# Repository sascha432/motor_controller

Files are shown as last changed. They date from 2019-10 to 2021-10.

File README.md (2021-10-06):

# DC Motor Controller with LED dimmer

Firmware for DC motor controller https://easyeda.com/sascha23095123423/dc-motor-controller

I am using this controller for a 500W drill press with a constant RPM from 300-4500rpm load independent

* Input voltage 13.5-40V
* DC Motor controller 20A continuously, 31.25kHz PWM
* 4A MOSFET driver
* Velocity mode, constant RPM from 150 up to 32000rpm
* PWM mode, duty cycle 5-100% (like regular drills)
* Opto Interrupter for RPM sensing
* Adjustable current limit 1-40A
* Adjustable auto stop if stalled for 250-5000ms
* Brake function with slow current decay
* ATmega328P PID controller for constant RPM
* LED driver 14-26V, 350mA, 10W, dimmable
* OLED display and rotary encoder, start/stop button
* Continuous motor current measurement and display (Ampere or Watt)
* Current limit indicator LED

## New Firmware 1.0.4

[Change Log v1.0.4](docs/CHANGELOG.md)

### Current PCB

[Schematics and Gerber Files](schematics/)

[https://oshwlab.com/sascha23095123423/dc-motor-controller](https://oshwlab.com/sascha23095123423/dc-motor-controller)
[https://oshwlab.com/sascha23095123423/dc-motor-controller-panel](https://oshwlab.com/sascha23095123423/dc-motor-controller-panel)

### Change Log PCB

### Rev1.4 & Rev1.5

* Motor current measurement
* MOSFET for the brake
* Improved DAC and current limit
* Improved LED dimmer
* IDC connector for the control panel (2x5P)
* JST PH connectors
* DTR connection for AVRDude/USB2Serial converters

### Rev1.3

* Current limit indicator LED
* Hardware circuit for current limit removed and overcurrent signal added to the MCU
* UCC27517DBVR MOSFET driver
* Kelvin connection to the shunt

### Rev1.1 & 1.2

* Input voltage detection
* PCB layout changes

### Rev1.0

* First prototype

## PCB and schematics

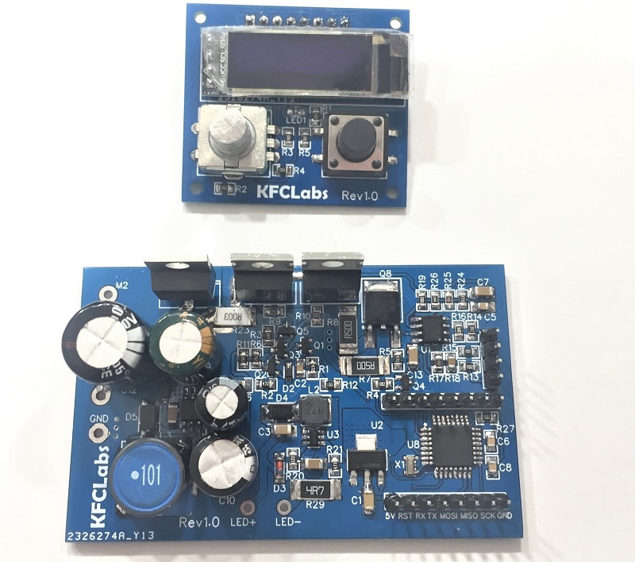
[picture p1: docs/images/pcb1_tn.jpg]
PCB Rev1.0


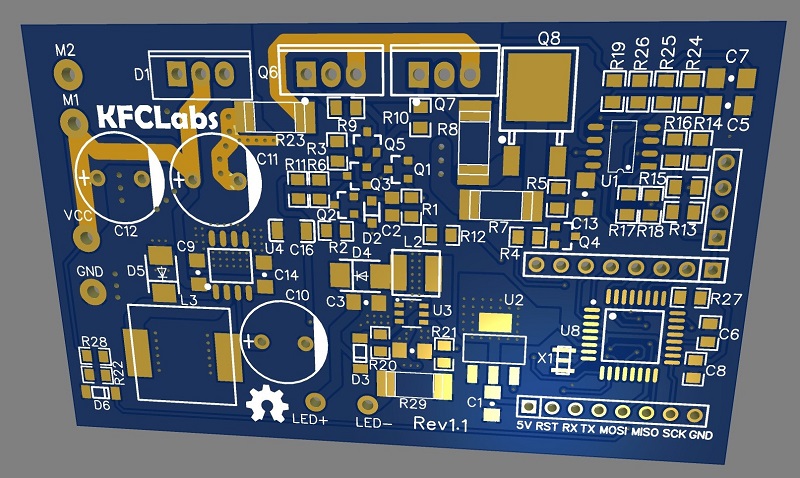
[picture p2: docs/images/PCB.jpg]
PCB


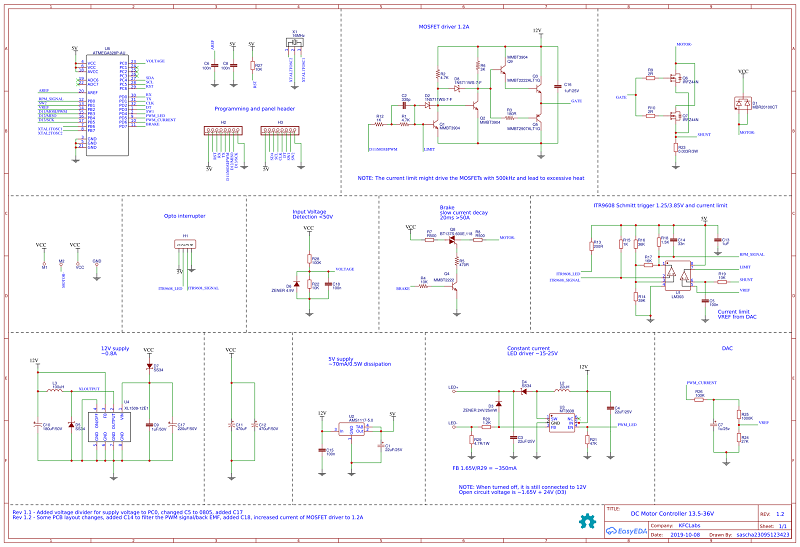
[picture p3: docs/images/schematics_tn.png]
Schematics


## First breadboard prototype

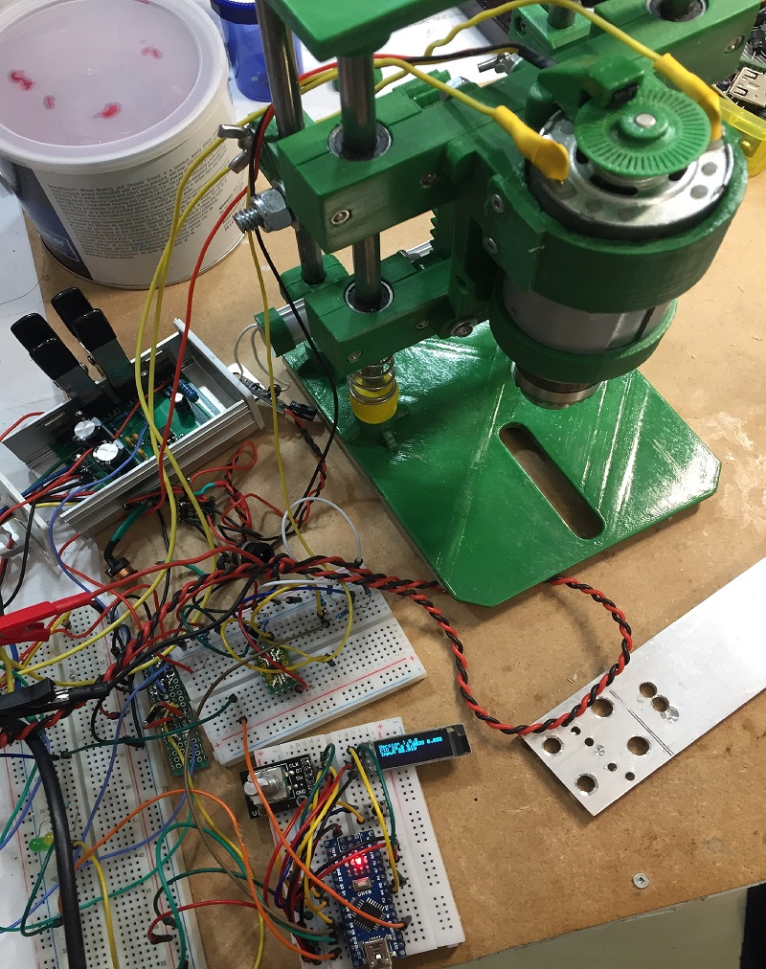
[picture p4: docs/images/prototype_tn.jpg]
Prototype


## STL files for the drill press

[Remix of a great drill press](https://www.thingiverse.com/thing:3693804)

[STL download](https://raw.githubusercontent.com/sascha432/motor_controller/master/stl/drill_press_stl.zip)

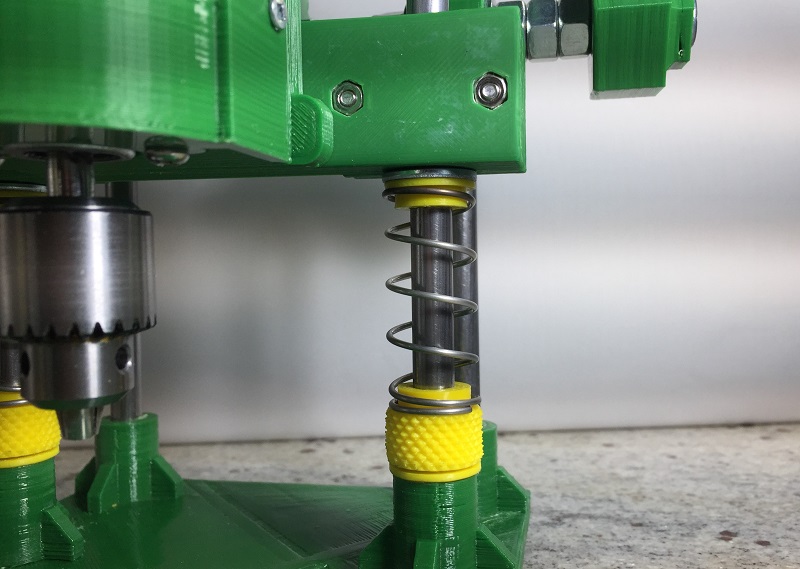
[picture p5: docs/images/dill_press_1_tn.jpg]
Drill press 1


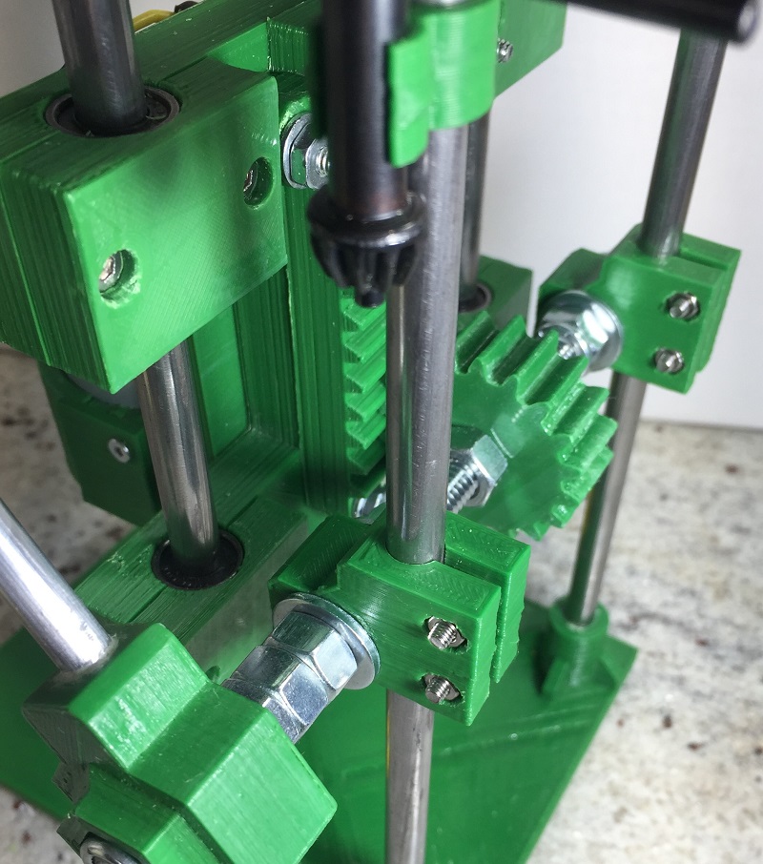
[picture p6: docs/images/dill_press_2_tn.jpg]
Drill press 2


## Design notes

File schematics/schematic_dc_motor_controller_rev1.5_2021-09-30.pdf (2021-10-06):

D11/MOSI/PWM

BRAKE

MOTOR-

IRF3205

Q6

IRF3205

Q7

GATE

6R

R9

6R

R10

GATE

MOTOR-

LM393

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
ITR9608_SIGNAL

ITR9608_LED

1K

R15
100R

R13

47K

R14

47K

R16

200K

R17

4.7K

R18

RPM_SIGNAL

M1

M2

16MHz

X1

1

2

3
XTAL2TOSC2

XTAL1TOSC1

AREF

5V
5V

100nF

C8
100nF

C6
33K

R27

XTAL2TOSC2

XTAL1TOSC1

AREF

5V

D13/SCK

D12/MISO

D11/MOSI/PWM

RST

TX

RX

ATMEGA328P-AU

U8

VCC 4
VCC 6
AVCC 18

ADC6 19
ADC7 22

AREF 20

PB0 12
PB1 13
PB2 14
PB3 15
PB4 16
PB5 17
PB6 7
PB7 8

GND 3
GND 5
GND 21

PC0 23
PC1 24
PC2 25
PC3 26
PC4 27
PC5 28
PC6 29

PD0 30
PD1 31
PD2 32
PD3 1
PD4 2
PD5 9
PD6 10
PD7 11

RPM_SIGNAL

SCL

SDA

CLK
DT
SW1

AMS1117-5.0

U2

In 3 | Out 2 GND

1

TAB 4

12V

22uF

C1

VCC

VCC

GND

4.7uF/50V

C3

MT3608

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
SS34

D4

12V

100K

R20
PWM_LED

47K

R21

LED-

LED+

I got the best results with 4.7uF, LEDs 21.6V@250mA and 120, 180 or 240Hz. With higher frequencies the dimming curve becomes non linear and the increase from duty cycle 96-100% is pretty steep (current 70-100%). There is no visible flicker and most cameras can filter multiples of 60Hz.
Using a lower output capacitor leads to overshoot at each PWM cycle
D6 is optional to prevent damage from overshoot. If the output capacitor is
too small, the diode will heat up.

22uF/25V

C4

22uH

L2

0.008R/3W

R23

10K

R19
SHUNT

VREF

VREF

10K

R25
100K

R26

PWM_CURRENT

10uF

C7

5V

XL1509-12E1

U4

VIN

1
OUTPUT

2

FB

3
ON/OFF

4 GND

5

GND

6

GND

7

GND

8

1uF/50V

C9
SS34

D5
180uF/50V

C10

12V | VCC

470uF

C11
470uF/50V

C12

XLOUTPUT

VCC

SHUNT

100uH/2A

L3

SBT40100VCT

D1

MOTOR-

VCC

1uF

C13

10uF

C16

SW2

PWM_LED
PWM_CURRENT
BRAKE

VREF

Brake / slow current decay
Adjust R8 that the current stays below the max. ratings of the MOSFET and motor

DAC for current limit detection
0-318mV, ~30 V ripple
200-300ms to reach the max. voltage @ 980Hz

MOSFET driver 4A

5V supply
~70mA/0.5W dissipation

12V supply
~110mA
With 10W of LEDs it goes up to 1.3A
If the LED driver is not used, it only requires a small inductor

ZENER 24V
D3

VCC

The original current limiter has been replaced and the LM393 sends a signal to the MCU. The rise time is <0.5ms

Current limit
VREF from DAC

VOLTAGE

Rev 1.1 - Added voltage divider for supply voltage to PC0, changed C5 to 0805, added C17
Rev 1.2 - Some PCB layout changes, added C14 to filter the PWM signal/back EMF, added C18, increased current of MOSFET driver to 1.2A, optional pullup R11 Rev 1.3 - Low cost 4A MOSFET driver UCC27517DBVR, Replaced R7 and R8 since they could not handle the braking current, replaced zener D6 with R31,
removed current limit circuit, connected current limit detection to D12/MISO, added proper trace from shunt to LM393, moved MOSFET driver away from shunt for better cooling, added LED output to PC1 Rev 1.4 - Improved LED dimming, current limit sensing and DAC, TO-220 TRIAC, C14 to filter noise from the opto interrupter
Rev 1.5 - Different connector for the control panel, JST PH wire to board connectors, removed R11, added PC3/ADC3, PE2/ADC6, PE3/ADC7 to headers, changed TRIAC brake to MOSFET, connection for DTR

VOLTAGE

VCC

2.7K

R22

100K

R28

Input Voltage Detection

Programming and panel header

Opto interrupter

A | A
B | B
C | C
D | D
E | E
F | F

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
TITLE:
DC Motor Controller 12-40V, 20A | REV: 1.5
Date: | 2019-10-08

Sheet: 1/1
Drawn By: sascha23095123423

Company: KFCLabs

100nF

C15

VCC

220uF/50V

C17

10nF

C18

NOTE: When turned off, it is still connected to 12V Open circuit voltage is ~26V

12V

MOTOR-

SHUNT

100nF

C2

UCC27517DBVR

U5

VDD 1
GND 2
IN+ 3
IN- 4
OUT 5

10K

R1

10K

R6

100K

R31

1R/5W

R8

10nF

C5

D12/MISO

4.7K

R4

Schmitt trigger for ITR9608 with 2.24/2.76V and current limit sensing

The current limit is supposed to signal over current to the MCU, not limit the actual current.

R9/10 limit the current to 4A @ 12V

LIMIT_LED

LIMIT_LED

300R

R7

31.25kHz PWM

# DC Motor Controller

- 13.5(12)-40V, 20A

## - Current limit sensing - 10W LED driver - Support for RPM measurement - PID controller for constant RPM

1uF

C20
6.8K

R12

1K

R24

100nF

C21

5.1R

R29
5.1R

R30
5.1R

R32

SHUNTMEAS

SHUNTMEAS

Optional constant current LED driver ~15-25V, PWM up to 1kHz

1nF

C14

BZT52C33

D6

RST

BSS138

MOTOR- | Q3

SS34

D2

### Remote Control Panel (OLED display, rotary encoder and buttons) https://oshwlab.com/sascha23095123423/dc-motor-controller-panel

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
9 10 10

5V

RST
RX
TX

D11/MOSI/PWM
D12/MISO
D13/SCK

B6B-PH-K-S(LF)(SN)

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
ITR9608_LED
ITR9608_SIGNAL

B10B-PH-K-S-(LF)(SN)

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
10 10

PC3

ADC7

ADC6

ADC6

PC3

ADC7

200K

R2

220K

R3

10K

R5

ZENER 15V

D7

IRF9540NPBF

Q1

DTR

DTR

10uF

C19

RST

DTR is for AVRDude/USB2Serial converters
If the reset pulse is too short, increase R27 and decrease it, if it is too long

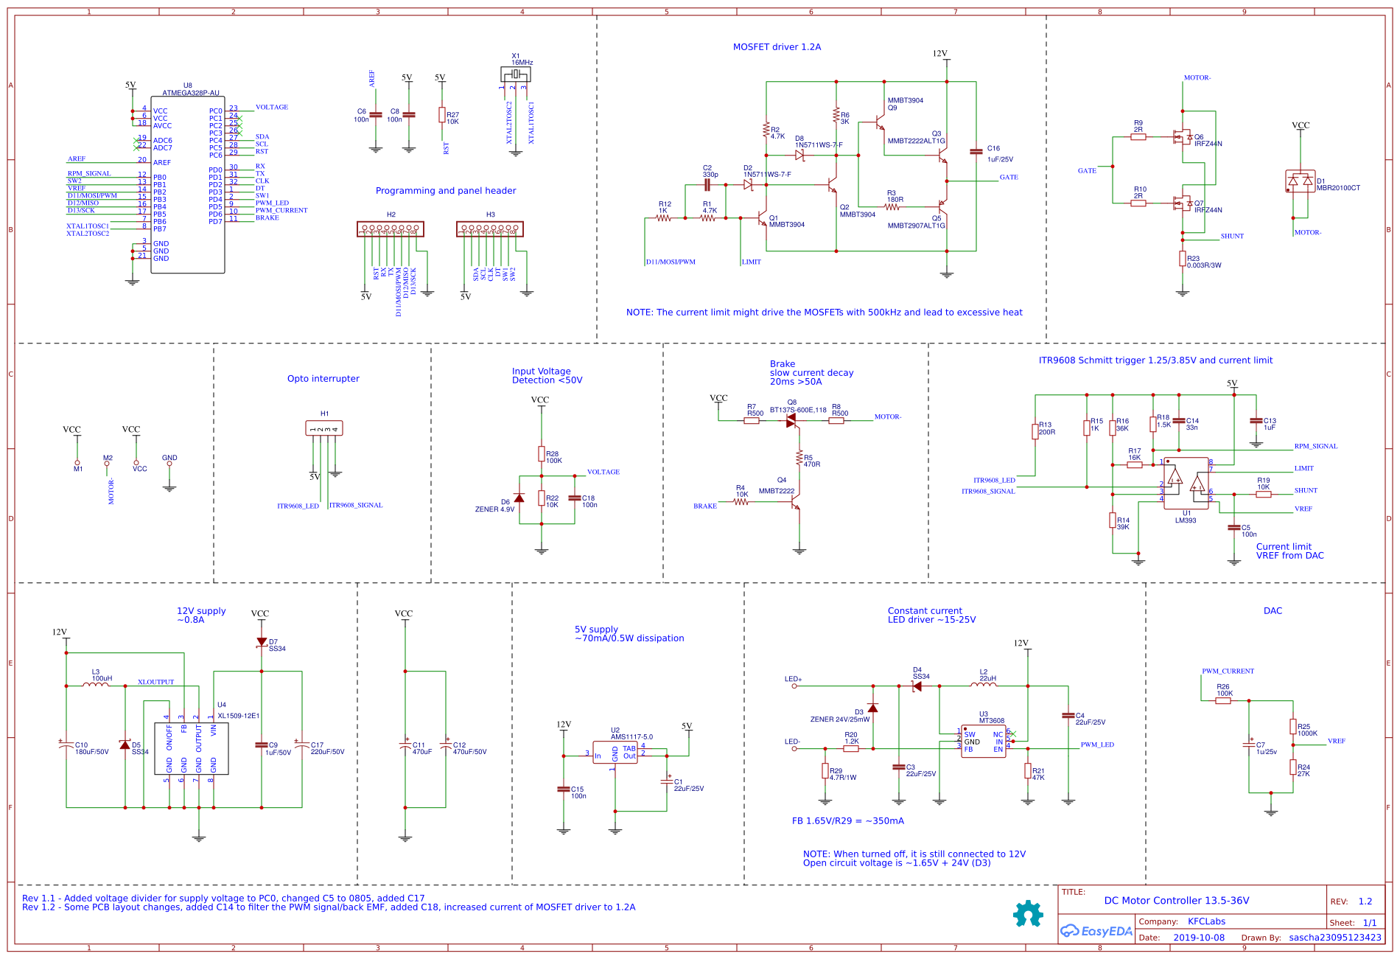
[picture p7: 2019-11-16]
docs/images/schematics.png

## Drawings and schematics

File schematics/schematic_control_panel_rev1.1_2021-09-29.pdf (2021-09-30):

## Control Panel with OLED display, rotary encoder and 2 buttons

## 5VSW¹ SW²

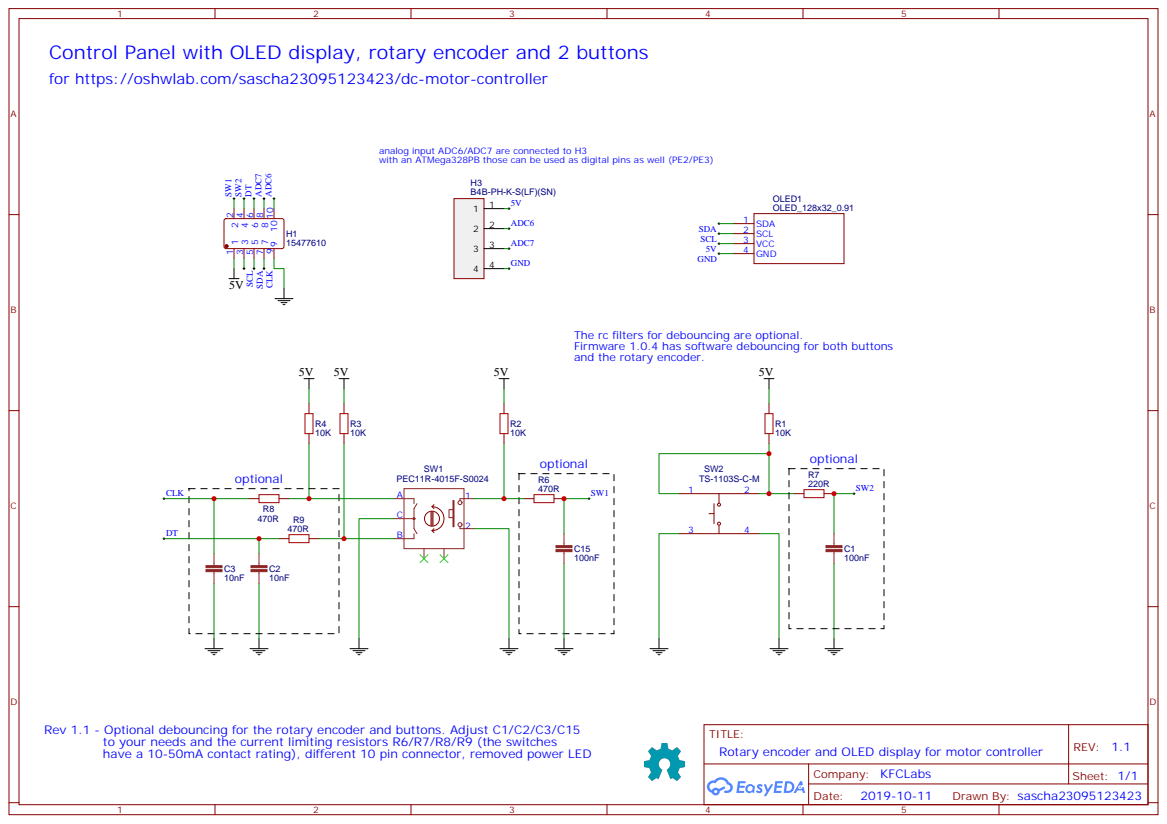
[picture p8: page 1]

for https://oshwlab.com/sascha23095123423/dc-motor-controller

analog input ADC6/ADC7 are connected to H3
with an ATMega328PB those can be used as digital pins as well (PE2/PE3)

The rc filters for debouncing are optional.
Firmware 1.0.4 has software debouncing for both buttons
and the rotary encoder.

Rev 1.1 - Optional debouncing for the rotary encoder and buttons. Adjust C1/C2/C3/C15

TITLE:
Rotary encoder and OLED display for motor controller

to your needs and the current limiting resistors R6/R7/R8/R9 (the switches
have a 10-50mA contact rating), different 10 pin connector, removed power LED

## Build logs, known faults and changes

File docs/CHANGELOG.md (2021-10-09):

# Changelog

## 1.0.5-dev

  - Fixed PWM mode running in velocity mode
  - Inverted current limit signal to match PCB Rev1.5
  - Improved current limit
  - Displaying average voltage to get rid of ADC noise
  - Fixed LED brightness display
  - Removed all dynamic memory allocations
  - Menu to select displaying Watt/Amps while the motor is running
  - Reduced overshoot of the PID controller after the current limit has been triggered

## 1.0.4

 - Using size optimized version of Adafruit SSD1306 to free 4.2KB flash memory
 - Using rising and falling edge for RPM detection to work more precisely
 - Reduced clock cycles required for the capture ISR
 - Added inline assembler for time critical parts
 - Reset defaults menu
 - Changed voltage detection analog reference to 1.1V
 - Reading buttons and rotary encoder via pin change interrupt
 - Display LED power
 - Implemented acceleration into the rotary encoder library
 - New rotary encoder algorithm with debouncing
 - Interrupt driven free running ADC
 - Replaced analogWrite to reduce code size
 - Display motor current or power while running
 - Enabled WDT while motor is running to turn it off if the software hangs
 - Rewritten the PID controller

## 1.0.3

- No display refresh with active current limit (I2C causes interferences with interrupts and timing issues)
- Current limit indicator LED
- Rewritten parts in C++
- Fixed issues with current limit in velocity mode

## 1.0.2

- Fixed displaying 0.0% RPM set point after reset
- Increased start duty cycle for velocity mode from 4% to 15%
- Max. PWM config option
- Improved current limit
- Tune PID settings menu while motor is running
- Dynamic averaging of the RPM sense pulses depending on the set RPM
- Improved menu acceleration
- Support for PCB Rev1.3
- Reduced min. RPM in velocity mode to 300

## 1.0.1

- Optimized code, ~2KB size reduction
- Brake enable/disable function
- Current limit indicator

## 1.0.0

- Initial version

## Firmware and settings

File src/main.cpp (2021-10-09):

/**
 * Author: sascha_lammers@gmx.de
 */

// DC motor controller with RPM feedback

#include <Arduino.h>
#include <SPI.h>
#include <Wire.h>
#include <EEPROM.h>
#include <Adafruit_SSD1306.h>
#include "main.h"
#include "rpm_sensing.h"
#include "interrupts.h"
#include "pid_control.h"
#include "motor.h"
#include "current_limit.h"
#include "timer.h"
#include "helpers.h"
#include "adc.h"
#include "serial_commands.h"

#if HAVE_COMPILED_ON_DATE
    const char __compile_date__[] PROGMEM = { __DATE__ " " __TIME__ };
#endif

ConfigData data;
UIConfigData ui_data;
Encoder knob(PIN_ROTARY_ENC_CLK, PIN_ROTARY_ENC_DT);
InterruptPushButton<PIN_BUTTON1_PORT, SFR::Pin<PIN_BUTTON1>::PINmask()> button1(PIN_BUTTON1, PRESSED_WHEN_LOW | ENABLE_INTERNAL_PULLUP);
InterruptPushButton<PIN_BUTTON2_PORT, SFR::Pin<PIN_BUTTON2>::PINmask()> button2(PIN_BUTTON2, PRESSED_WHEN_LOW | ENABLE_INTERNAL_PULLUP);

#if (ADAFRUIT_SSD1306_FIXED_SIZE == 0) || (ADAFRUIT_SSD1306_FIXED_WIDTH != SCREEN_WIDTH || ADAFRUIT_SSD1306_FIXED_HEIGHT != SCREEN_HEIGHT)
#    error invalid settings
#endif

static const char menuItemsString[] PROGMEM = { MENU_ITEMS_STRING };

Adafruit_SSD1306 display(OLED_ADDRESS, OLED_RESET_PIN);
Menu menu;

void read_eeprom()
{
    EEPROMData eeprom_data;
    EEPROM.get(0, eeprom_data);
    if (eeprom_data.magic == EEPROM_MAGIC) {
        data = eeprom_data;
        pid.setPidValues(eeprom_data.pid_settings);
    }
}

void write_eeprom(const __FlashStringHelper *message)
{
    EEPROMData eeprom_data, eeprom_data_current;

    if (message == nullptr) {
        message = F("SAVED");
    }

    eeprom_data.magic = EEPROM_MAGIC;
    eeprom_data = data;
    eeprom_data.pid_settings = pid.getPidValues();

    EEPROM.get(0, eeprom_data_current);
    if (eeprom_data != eeprom_data_current) {
        EEPROM.put(0, eeprom_data);
        display_message(message, Timeouts::Menu::kSaved);
    }
    else {
        menu.close();
    }
}

void set_version(char *buffer)
{
    sprintf_P(buffer, PSTR("Version %u.%u.%u"), VERSION_MAJOR, VERSION_MINOR, VERSION_PATCH);
}

#if HAVE_LED

void _ledBrightness_str(char *message, uint8_t size)
{
    if (data.getLedBrightness() < LED_MIN_PWM) {
        strcpy_P(message, PSTR("OFF"));
    }
    else {
        PrintBuffer buf(message, size);
        buf.print(data.getLedBrightessPercent(), 1);
        buf.println('%');
    }
}

#endif

#if HAVE_CURRENT_LIMIT

void current_limit_str(char *message, uint8_t size)
{
    if (current_limit.isDisabled()) {
        strcpy_P(message, PSTR("DISABLED"));
    }
    else {
        PrintBuffer buf(message, size);
        buf.print(current_limit.getLimitAmps(), 1);
        buf.print('A');
    }
}

#endif

void setup()
{
    motor.begin();
    setupLedPwm();

    Serial.begin(115200);

    current_limit.begin();

    #if HAVE_VOLTAGE_DETECTION
        asm volatile ("cbi %0, %1" :: "I" (SFR::Pin<PIN_VOLTAGE>::DDR_IO_ADDR()), "I" (SFR::Pin<PIN_VOLTAGE>::PINbit()));
    #endif
    #if HAVE_CURRENT_DETECTION
        asm volatile ("cbi %0, %1" :: "I" (SFR::Pin<PIN_CURRENT>::DDR_IO_ADDR()), "I" (SFR::Pin<PIN_CURRENT>::PINbit()));
    #endif
    #if HAVE_VOLTAGE_DETECTION || HAVE_CURRENT_DETECTION
        adc.begin();
    #endif

    button1.onPress(start_stop_button_pressed);
    button2.onRelease(rotary_button_released);

    read_eeprom();
    setup_display();
    menu.add(menuItemsString);

    ATOMIC_BLOCK(ATOMIC_FORCEON) {
        TCCR1A = 0;
        TCCR1B = TIMER1_PRESCALER_BV;
        TCCR2B = (TCCR2B & 0b11111000) | TIMER2_PRESCALER_BV;
        rpm_sense.begin();
        setup_interrupts();
    }

    char message[32];
    set_version(message);
    Serial.println(message);
    #if HAVE_COMPILED_ON_DATE
        Serial.print(F("Compiled on "));
        Serial.println(FPSTR(__compile_date__));
    #endif
    display_message(message, Timeouts::kVersion, 1);

    knob.setAcceleration(KNOB_ACCELERATION);
}

void process_ui_events()
{
    PinChangesEnum tmpFlag;
    ATOMIC_BLOCK(ATOMIC_FORCEON) {
        tmpFlag = pinChangedFlag;
        pinChangedFlag = PinChangedType::NONE;
    }
    if (ui_data.isTimeoutOnce()) {
        // ignore events during delay
        return;
    }

    if (tmpFlag & PinChangedType::BUTTON1) {
        button1.update();
    }
    if (tmpFlag & PinChangedType::BUTTON2) {
        button2.update();
    }
    if (tmpFlag & PinChangedType::KNOB) {
        read_rotary_encoder();
    }
}


void loop() {

    serial_commands();
    process_ui_events();
    data.loop();
    motor.loop();
    menu.loop();
    ui_data.loop();
    display_refresh();

    #if 0

    static uint16_t debugIimer;
    if (micros16() - debugIimer >= 5000) {
        debugIimer = micros16();

        static int16_t dc = -1;
        if (motor.isOn()) {
            if (dc == -1) {
                dc = 0;
                pid.printValues(Serial);
                Serial.print(F("start "));
                Serial.println(data.getSetPointRPM());
            }
            uint32_t t = micros() - motor._startTime;
            if (dc != pid.getDutyCycle()) {
                if (Serial.availableForWrite() > 24) {
                    dc = pid.getDutyCycle();
                    Serial.print(t);
                    Serial.print(',');
                    Serial.print(ui_data.getRpm());
                    Serial.print(',');
                    Serial.print(dc);
                    Serial.print('\n');
                }
            }
            else if (ui_data.getRpm() == data.getSetPointRPM() || t > 2 * 1000000) {
                // Serial.println(F("end"));
                // motor.stop(MotorStateEnum::OFF);
            }
        }
        else {
            dc = -1;
        }
    }
    #endif
}

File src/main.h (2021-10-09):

/**
 * Author: sascha_lammers@gmx.de
 */

#pragma once

#include <Arduino.h>
#include <util/atomic.h>
#include <wiring_private.h>
#include <avr/wdt.h>
#include <Button.h>
#include <ButtonEventCallback.h>
#include <PushButton.h>
#include <Bounce2.h>
#include <Encoder.h>
#include <Adafruit_SSD1306.h>
#include "helpers.h"
#include "avr_reg.h"
#include "int24_types.h"

#define VERSION_MAJOR                           1
#define VERSION_MINOR                           0
#define VERSION_PATCH                           5

// show at what time and date the firmware was compiled
#ifndef HAVE_COMPILED_ON_DATE
#define HAVE_COMPILED_ON_DATE                   1
#endif

#if DEBUG
#define DEBUG_INPUTS                            0
#define DEBUG_MOTOR_SPEED                       0
#define DEBUG_PID_CONTROLLER                    0
#else
#define DEBUG_INPUTS                            0
#define DEBUG_MOTOR_SPEED                       0
#define DEBUG_PID_CONTROLLER                    0
#endif

// enable serial commands
// >2700 byte (includes HAVE_SERIAL_HELP, HAVE_SERIAL_MOTOR_CONTROL, HAVE_VOLTAGE_DETECTION etc...)
#ifndef HAVE_SERIAL_COMMANDS
#define HAVE_SERIAL_COMMANDS                    1
#endif

// disable LED support
#ifndef HAVE_LED
#define HAVE_LED                                1
#endif

// enable serial commands
// ~344 byte
#ifndef HAVE_SERIAL_MOTOR_CONTROL
#define HAVE_SERIAL_MOTOR_CONTROL               0
#endif

// read supply voltage from ADC
// ~572byte
#ifndef HAVE_VOLTAGE_DETECTION
#define HAVE_VOLTAGE_DETECTION                  1
#endif

// read motor current from ADC
// ~300 byte
#ifndef HAVE_CURRENT_DETECTION
#define HAVE_CURRENT_DETECTION                  1
#endif

// have pin that signals overcurrent
// ~816 byte
#ifndef HAVE_CURRENT_LIMIT
#define HAVE_CURRENT_LIMIT                      1
#endif

// display power consumption of the LEDs
// ~434 byte
#ifndef HAVE_LED_POWER
#define HAVE_LED_POWER                          0
#endif

#if !HAVE_LED
#undef HAVE_LED_POWER
#define HAVE_LED_POWER 0
#endif

// pins

// D11/PB3/15
// pin for the mosfet driver. analogWrite is pretty slow (and adds quite some extra code)
#define PIN_MOTOR_PWM                           11
#define PIN_MOTOR_ENABLE_PWM()                  sbi(_SFR_MEM8(SFR::Pin<PIN_MOTOR_PWM>::TCCR_MEM_ADDR()), SFR::Pin<PIN_MOTOR_PWM>::TCCRbit())
#define PIN_MOTOR_DISABLE_PWM()                 cbi(_SFR_MEM8(SFR::Pin<PIN_MOTOR_PWM>::TCCR_MEM_ADDR()), SFR::Pin<PIN_MOTOR_PWM>::TCCRbit())

inline void stopMotor()
{
    PIN_MOTOR_DISABLE_PWM();
    SFR::Pin<PIN_MOTOR_PWM>::OCR() = 0;
    asm volatile ("cbi %0, %1" :: "I" (SFR::Pin<PIN_MOTOR_PWM>::PORT_IO_ADDR()), "I" (SFR::Pin<PIN_MOTOR_PWM>::PINbit()));     // digital write low
}

inline void setupMotorPwm()
{
    asm volatile ("cbi %0, %1" :: "I" (SFR::Pin<PIN_MOTOR_PWM>::PORT_IO_ADDR()), "I" (SFR::Pin<PIN_MOTOR_PWM>::PINbit()));     // digital write low
    asm volatile ("sbi %0, %1" :: "I" (SFR::Pin<PIN_MOTOR_PWM>::DDR_IO_ADDR()), "I" (SFR::Pin<PIN_MOTOR_PWM>::PINbit()));      // pin mode
    SFR::Pin<PIN_MOTOR_PWM>::OCR() = 0;
}

inline void stopMotorAtomic()
{
    ATOMIC_BLOCK(ATOMIC_RESTORESTATE) {
        stopMotor();
    }
}

// do not use for 0 (stopMotor) or 255 (setMotorPWMAtomic)
// PWM must be enabled
inline void setMotorPWM_timer(uint8_t pwm)
{
    SFR::Pin<PIN_MOTOR_PWM>::OCR() = pwm; // analog write
}

// returns 0 if the motor is off and 255 if running at 100% duty cycle
inline uint8_t getMotorPWM_timer()
{
    return SFR::Pin<PIN_MOTOR_PWM>::OCR();
}

// use stopMotor() for pwm = 0
inline void setMotorPWM(uint8_t pwm)
{
    if (pwm == 0) {
        stopMotor();
    }
    else if (pwm == 255) {
        PIN_MOTOR_DISABLE_PWM();
        SFR::Pin<PIN_MOTOR_PWM>::OCR() = 255;
        asm volatile ("sbi %0, %1" :: "I" (SFR::Pin<PIN_MOTOR_PWM>::PORT_IO_ADDR()), "I" (SFR::Pin<PIN_MOTOR_PWM>::PINbit())); // digital write high
    }
    else {
        setMotorPWM_timer(pwm);
        PIN_MOTOR_ENABLE_PWM();
    }
}

inline void setMotorPWMAtomic(uint8_t pwm)
{
    ATOMIC_BLOCK(ATOMIC_RESTORESTATE) {
        setMotorPWM(pwm);
    }
}


// D7/PD7/11
// pin to enable the brake. it basically shorts the motor wires for slow current decay
// it is important that the mosfets are turned off before the break is engaged + a short delay depending
// on the mosfet driver. having the mosfets on and the brake engaged will cause a dead short
#define PIN_BRAKE                               7

inline bool isBrakeOn()
{
    asm volatile goto (
        "sbic %0, %1\n\t"
        "rjmp %l[BRAKE_ENABLED]\n\t"
        :: "I" (SFR::Pin<PIN_BRAKE>::PIN_IO_ADDR()), "I" (SFR::Pin<PIN_BRAKE>::PINbit()) :: BRAKE_ENABLED
    );
    return false;

BRAKE_ENABLED:
    return true;
}

inline void setBrakeOn()
{
    asm volatile ("sbi %0, %1" :: "I" (SFR::Pin<PIN_BRAKE>::PORT_IO_ADDR()), "I" (SFR::Pin<PIN_BRAKE>::PINbit()));
}
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

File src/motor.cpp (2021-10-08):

    /**
 * Author: sascha_lammers@gmx.de
 */

#include <avr/wdt.h>
#include "main.h"
#include "motor.h"
#include "interrupts.h"
#include "pid_control.h"
#include "rpm_sensing.h"
#include "current_limit.h"
#include "adc.h"

Motor motor;

void Motor::loop()
{
    if (motor.isOn()) {

        // check if the RPM signal has not been updated for a given period of time
        auto last = rpm_sense.getLastSignalTicks();
        if (last > _maxStallTime * Timer1::kTicksPerMillisecond) {
            // Serial.print(F("last signal "));
            // Serial.println(last/Timer1::kTicksPerMillisecond);
            #if DEBUG_MOTOR_SPEED
                if (motor.isOn()) {
                    Serial.printf_P(PSTR("dur=%lu max=%u\n"), dur, _maxStallTime);
                }
            #endif

            if (motor.isOn()) {
                stop(MotorStateEnum::STALLED);
            }
            else if (isBrakeOn()) { // release brake
                setBrake(false);
                if (menu.isClosed()) {
                    ui_data.refreshDisplay();
                }
            }
        }

        wdt_reset();
    }
}

void Motor::start()
{
    // if (isBrakeOn()) {
    //     // if the brake is still engaged, for example when turning the motor off and on quickly
    //     // turn the brake off, update the display and wait 100ms
    //     #if DEBUG_MOTOR_SPEED
    //         Serial.print(F("brake_on"));
    //     #endif
    //     setBrake(false);
    //     ui_data.refreshDisplay();
    //     refresh_display();
    //     delay(100);

    //     // make sure it is off
    //     if (isBrakeOn()) {
    //         stop(MotorStateEnum::ERROR);
    //         return;
    //     }
    // }
    setBrake(false);

    ATOMIC_BLOCK(ATOMIC_FORCEON) {
        // enable WDT to restart in case of a crash while the motor is running
        wdt_enable(WDTO_1S);

        // reset ui data
        ui_data = {};
        _state = MotorStateEnum::ON;
        // _startTime = micros();

        // reset rpm sensing and pid controller
        rpm_sense.reset();
        pid.reset();

        // reset / enable current limit
        current_limit.enable();

        // set motor speed
        if (isDutyCycleMode()) {
            setSpeed(data.getSetPointDutyCycle());
        }
        else {
            setSpeed(START_DUTY_CYCLE_PID);
        }
    }
    ui_data.refreshDisplay();
}

void Motor::stop(MotorStateEnum state)
{
    ATOMIC_BLOCK(ATOMIC_RESTORESTATE) {
        _state = state;
        setSpeed(0);
        current_limit.disable();
    }

    const __FlashStringHelper *message;
    switch (state) {
        case MotorStateEnum::ERROR:
            message = F("ERROR");
            break;
        case MotorStateEnum::STALLED:
            message = F("STALLED");
            break;
        case MotorStateEnum::OFF:
            message = F("OFF");
            break;
        default:
            message = motor.isBrakeEnabled() ? F("BRAKING") : F("OFF");
            break;
    }
    display_message(message, Timeouts::Menu::kMessage);
    data.pidConfig() = PidConfigEnum::OFF;

    wdt_disable();
}

// set PWM duty cycle with enabling/disabling the brake and turning the motor signal led on/off
// called inside ISR
// the PID controller does not use this method
void Motor::setSpeed(uint8_t speed)
{
    #if DEBUG
        if (!isOn() && speed != 0) {
            #if DEBUG_MOTOR_SPEED
                Serial.print(F("error_speed"));
            #endif
            stop(MotorStateEnum::ERROR);
            return;
        }
    #endif
    if (speed > _maxPWM) {
        speed = _maxPWM;
    }
    if (speed != 0) {
        if (isBrakeOn()) {
            #if DEBUG_MOTOR_SPEED
                Serial.print(F("error_brake"));
            #endif
            stop(MotorStateEnum::ERROR);
            return;
        }
        speed = current_limit.getDutyCycle(speed);
        #if DEBUG_MOTOR_SPEED
            Serial.printf_P(PSTR("speed=%u\n"), (int)speed);
        #endif
        setMotorPWMAtomic(speed);
    }
    else if (speed == 0) {
        ATOMIC_BLOCK(ATOMIC_RESTORESTATE) {
            if (isOn()) {
                #if DEBUG_MOTOR_SPEED
                    Serial.printf_P(PSTR("set_mode=%u\n"), (int)_mode);
                #endif
                _state = MotorStateEnum::OFF;
            }
        }
        // turns motor off as well
        setBrake(true);
    }
}

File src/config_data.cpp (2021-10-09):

/**
 * Author: sascha_lammers@gmx.de
 */

#include "main.h"
#include "rpm_sensing.h"
#include "pid_control.h"
#include "motor.h"
#include "current_limit.h"
#include "config_data.h"

ConfigData::ConfigData() :
    pid_config(PidConfigEnum::OFF),
    #if HAVE_RPM_PER_VOLT
        rpm_per_volt(300),
    #endif
    #if HAVE_LED
        _ledBrightness(30 * 255 / LED_MAX_PWM),
        _ledBrightnessPwm(0),
        _ledFadeTimer(0),
    #endif
    _setPointDutyCycle(30 * 100 / MAX_DUTY_CYCLE),
    _setPointRpm(1000),
    _setPointTicks(RPM_SENSE_RPM_TO_TICKS(1000)),
    _motorStatus(MotorStatusEnum::WATT)
{
}

EEPROMData &EEPROMData::operator=(const ConfigData &data)
{
    control_mode = motor.getMode();

    set_point_rpm = data.getSetPointRPM();
    set_point_pwm = data.getSetPointDutyCycle();
    _motorStatus = data.getDisplayMotorStatus();
    #if HAVE_LED
        _ledBrightness = data.getLedBrightness();
    #endif
    #if HAVE_CURRENT_LIMIT
        current_limit = ::current_limit.getLimit();
    #endif
    brake_enabled = motor.isBrakeEnabled();
    max_stall_time = motor.getMaxStallTime();
    max_pwm = motor.getMaxDutyCycle();
    #if HAVE_RPM_PER_VOLT
        rpm_per_volt = data.getRpmPerVolt();
    #endif
    return *this;
}

ConfigData &ConfigData::operator=(const EEPROMData &eeprom_data)
{
    setSetPointDutyCycle(eeprom_data.set_point_pwm);
    setSetPointRPM(eeprom_data.set_point_rpm);
    setDisplayMotorStatus(eeprom_data._motorStatus);
    #if HAVE_LED
        _ledBrightness = eeprom_data._ledBrightness;
        _ledBrightnessPwm = 0;
        _ledFadeTimer = 0;
    #endif
    #if HAVE_CURRENT_LIMIT
        current_limit.setLimit(eeprom_data.current_limit);
    #endif
    motor.setMaxStallTime(eeprom_data.max_stall_time);
    motor.enableBrake(eeprom_data.brake_enabled);
    motor.setMaxDutyCycle(eeprom_data.max_pwm);
    motor.setMode(eeprom_data.control_mode);
    #if HAVE_RPM_PER_VOLT
        data.setRpmPerVolt(eeprom_data.rpm_per_volt);
    #endif
    return *this;
}

void ConfigData::changeSetPoint(int16_t value)
{
    if (motor.isVelocityMode()) {
        setSetPointRPM(getSetPointRPM() + KNOB_GET_VALUE(value, KNOB_VALUE_SPEED));
    }
    else {
        setSetPointDutyCycle(std::clamp<int16_t>(getSetPointDutyCycle() + KNOB_GET_VALUE(value, KNOB_VALUE_SPEED), MIN_DUTY_CYCLE, MAX_DUTY_CYCLE));
        if (motor.isOn()) {
            motor.setSpeed(getSetPointDutyCycle());
        }
    }
}

#if HAVE_LED

bool ConfigData::updateLedBrightness()
{
    if (_ledBrightnessPwm != _ledBrightness) {
        if (_ledBrightnessPwm < _ledBrightness) {
            _ledBrightnessPwm++;
        }
        else if (_ledBrightnessPwm > _ledBrightness) {
            _ledBrightnessPwm--;
        }
    }
    analogWriteLedPwm(_ledBrightnessPwm);
    return _ledBrightnessPwm != _ledBrightness;
}

#endif

void ConfigData::loop()
{
#if HAVE_LED
    auto millis = millis16();
    if (millis - _ledFadeTimer >= LED_FADE_TIME) {
        _ledFadeTimer = millis;
        updateLedBrightness();
    }
#endif
}

void UIConfigData::loop()
{
    auto millis = millis16();
    if (millis - _updateUITimer >= Timeouts::Display::kRefresh) {
        _updateUITimer = millis;
        updateRpmAndDutyCycle();
    }
}

void UIConfigData::updateRpmAndDutyCycle()
{
    auto events = rpm_sense.getEvents();
    if (events._count) {
        _displayRpm = (static_cast<uint32_t>(_displayRpm) + events._ticks) / (events._count + 1);
    }
    _dutyCycleAvg = ((static_cast<uint16_t>(_dutyCycleAvg) << 2) + getMotorPWM_timer()) / 5;
}

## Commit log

2019-10-19 STL files
2019-11-16 Matched pins to PCB
2020-06-07 reduced code size and some fixes
    [data_t.cpp, main.cpp, main.h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]
2020-06-09 fixed setting Kd variable
    [pid_control.cpp]
2020-06-09 fixed LED brightness and added variable to store pwm/velocity separately
    [data_t.cpp, main.cpp, main.h]
2021-08-28 measure rpm per volt/duty cycle
2021-09-15 replaced reference with global, pass menu as a single string
    [menu.cpp]
2021-09-15 proper Serial.printf support
2021-09-16 fixes and LED power display
    [current_limit.h, data_t.cpp, main.cpp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]
2021-09-17 improved rotary encoder
2021-09-19 printf optimized
2021-09-20 interrupt driven free running ADC
2021-09-20 fixed current limit calculations
    [main.cpp, main.h]
2021-09-20 optimized DAC/ADC calculations
2021-09-21 display motor current while running
2021-09-22 current shunt offset
2021-09-30 schematics and gerber files
    [Gerber_BoardOutline.GKO, Gerber_BottomLayer.GBL, Gerber_BottomSilkLayer.GBO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]
2021-09-30 schematics and gerber files, readme update
    [Gerber_BoardOutline.GKO, Gerber_BottomLayer.GBL, Gerber_BottomSilkLayer.GBO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]
2021-09-30 timer triggered ADC reading
2021-09-30 fixed current limit
2021-09-30 code cleanup after fixing current limit
    [config_data.cpp, current_limit.h, main.cpp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]
2021-10-03 new PID controller and code cleanup
2021-10-06 pid controller and rpm sensing improved
2021-10-06 version 1.0.4
    [Gerber_BoardOutline.GKO, Gerber_BottomLayer.GBL, Gerber_BottomSolderMaskLayer.GBS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]
2021-10-08 improved current limit
2021-10-08 voltage averaging
2021-10-09 reset device if the display cannot be initialized
    [main.cpp]
2021-10-09 fixed LED display range
    [main.h]
2021-10-09 menu to select displaying Watt/Amps while the motor is running
2021-10-09 reduce overshoot after the current limit has been triggered
    [current_limit.h, pid_control.cpp]
2021-10-09 code cleanup and displaying watt while selecting LED brightness
